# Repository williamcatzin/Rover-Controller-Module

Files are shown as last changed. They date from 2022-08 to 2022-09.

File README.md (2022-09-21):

# **Rover Controller Module**

The Rover Controller Module is an electronic control module (ECM) for a Mars rover prototype being developed by the AI Rover team from the Space Technologies At Cal (STAC). The PCB is a four-layer board consisting of an ESP32-WROOM32 module, BMI088 IMU breakout board, RFM69HCW transceiver module, UART header pin interface for three Roboclaw 2x7A motor controllers, and a SPI header pin interface for an external microprocessor such as an NVIDIA Jetson or Raspberry Pi. There’s also decoupling capacitors to suppress power supply noise and TVS diodes for safety and component protection. The PCB was designed using KiCAD and manufactured by JLCPCB. Top and bottom layers are signal planes. First middle layer is the ground plane and the second middle layer is the power plane. I've also placed three test points at the UART, I2C, and SPI serial buses respectively, mounting holes, and logos for aesthetics. Here’s the Rover Controller Module v1.

|||
|:-:|:-:|
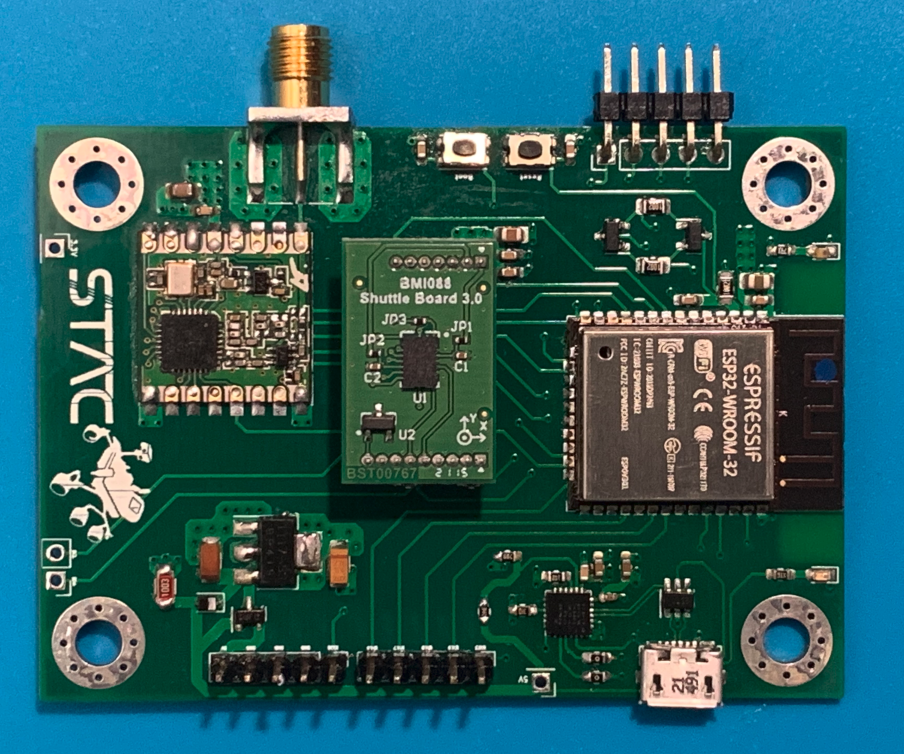
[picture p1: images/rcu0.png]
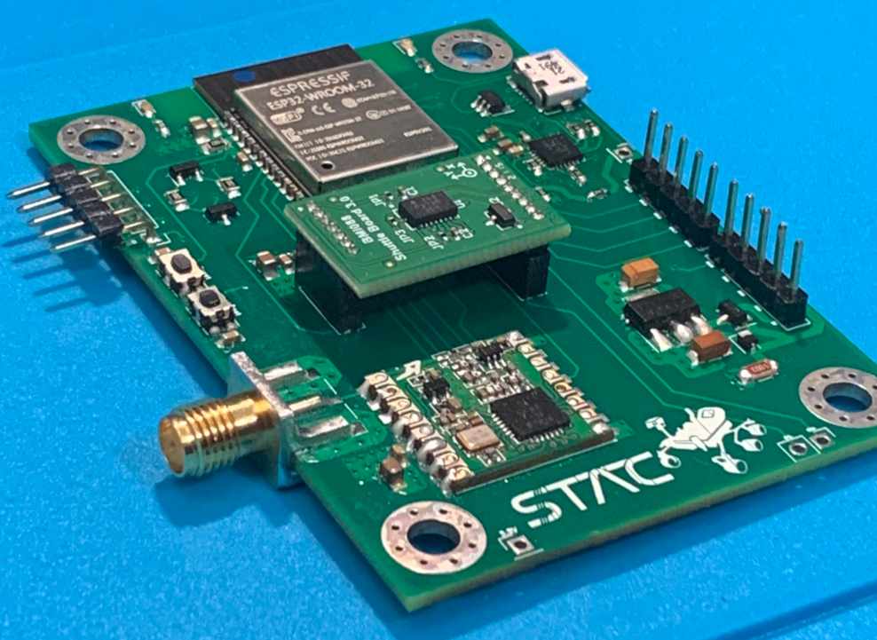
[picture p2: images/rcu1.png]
|||

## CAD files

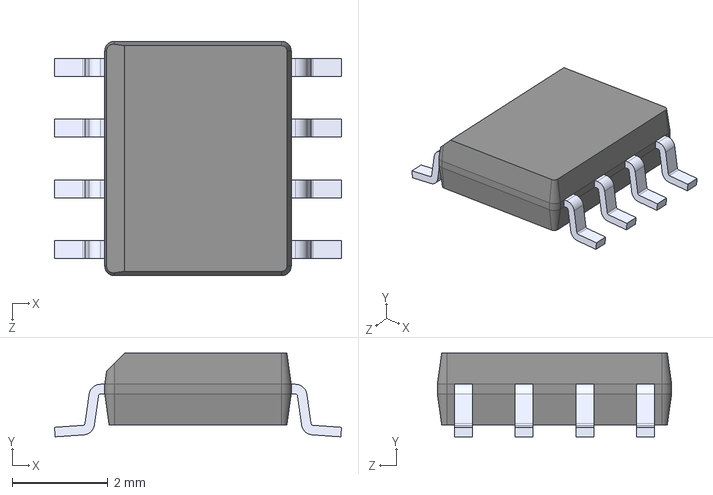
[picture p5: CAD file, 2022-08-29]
pcb_workspace/rover_controller/Regulator/SOIC127P600X175-8N.step
6.00 x 1.75 x 4.90 mm

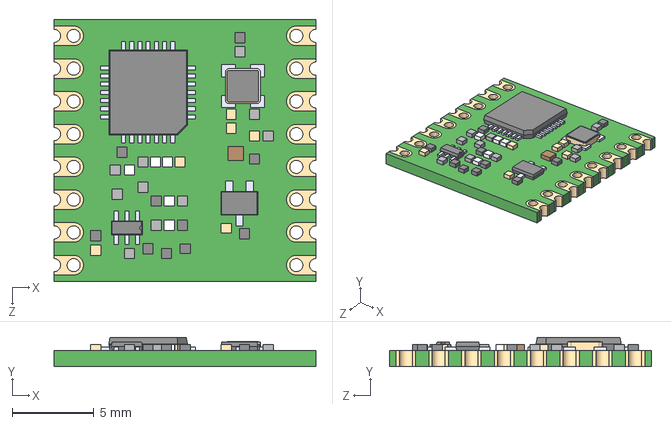
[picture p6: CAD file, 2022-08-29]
pcb_workspace/rover_controller/RFM69HCW/COM-13909.step
16.0 x 1.80 x 16.0 mm

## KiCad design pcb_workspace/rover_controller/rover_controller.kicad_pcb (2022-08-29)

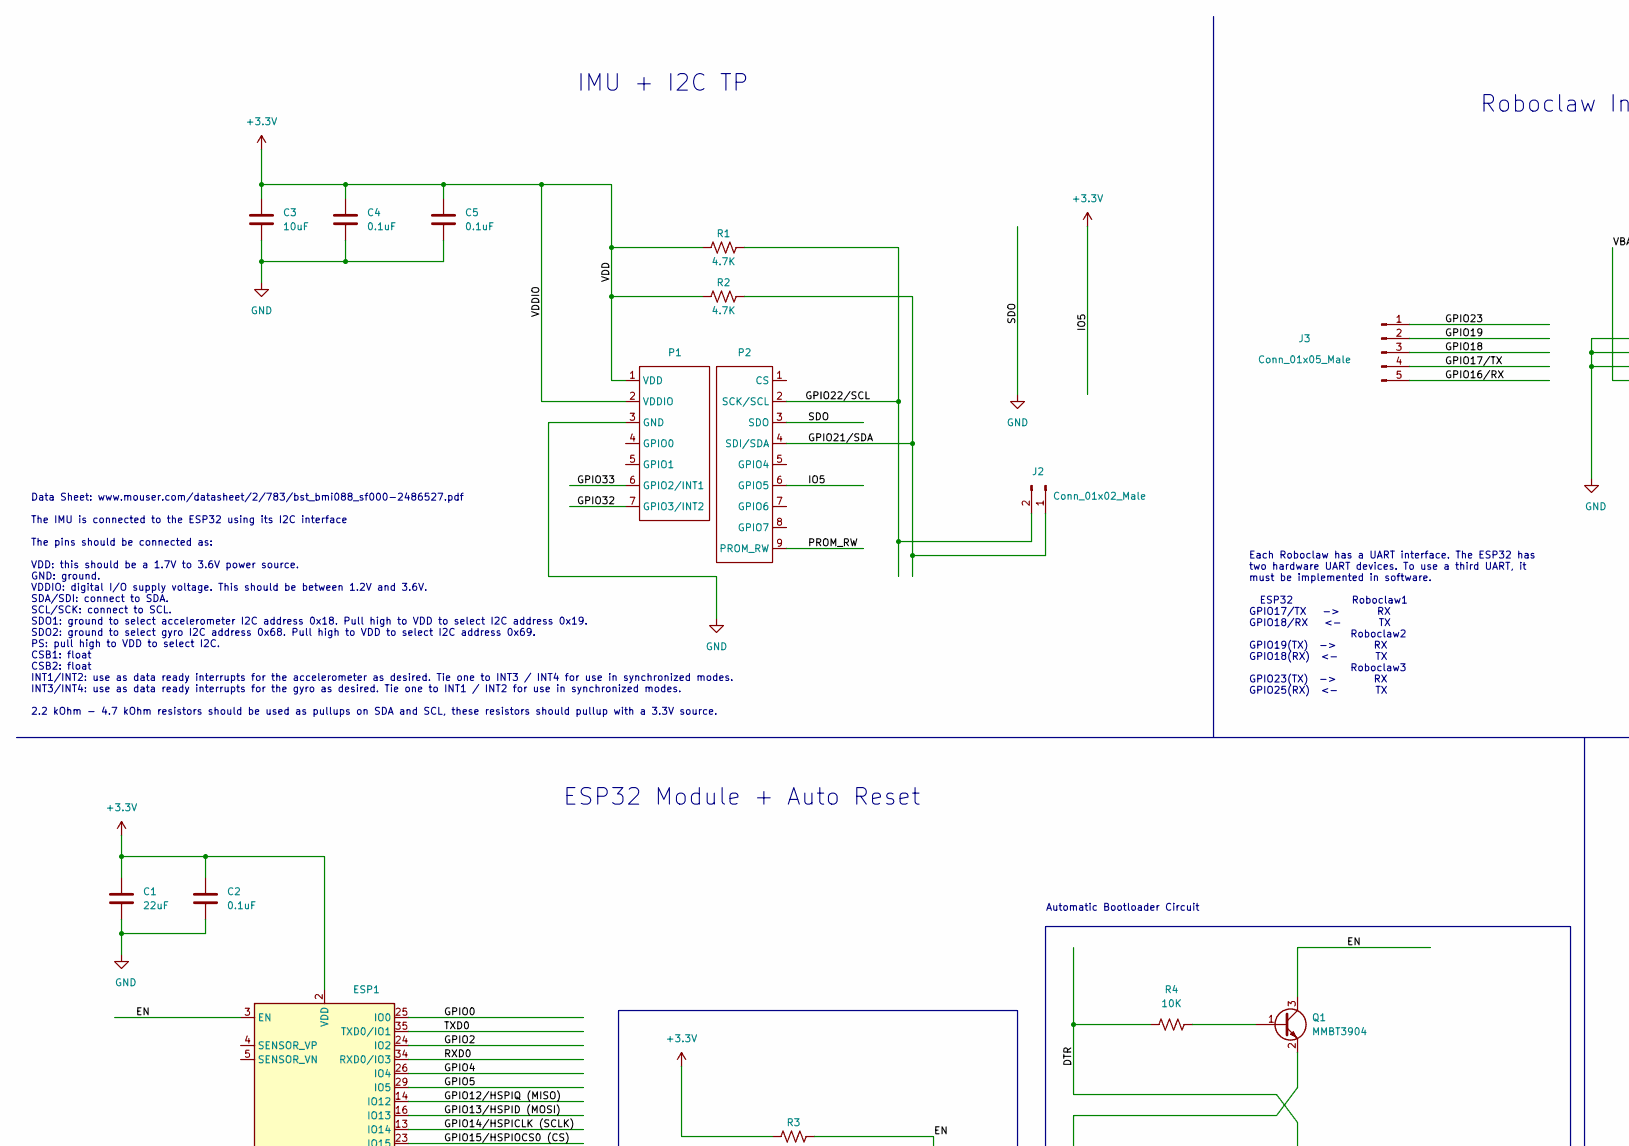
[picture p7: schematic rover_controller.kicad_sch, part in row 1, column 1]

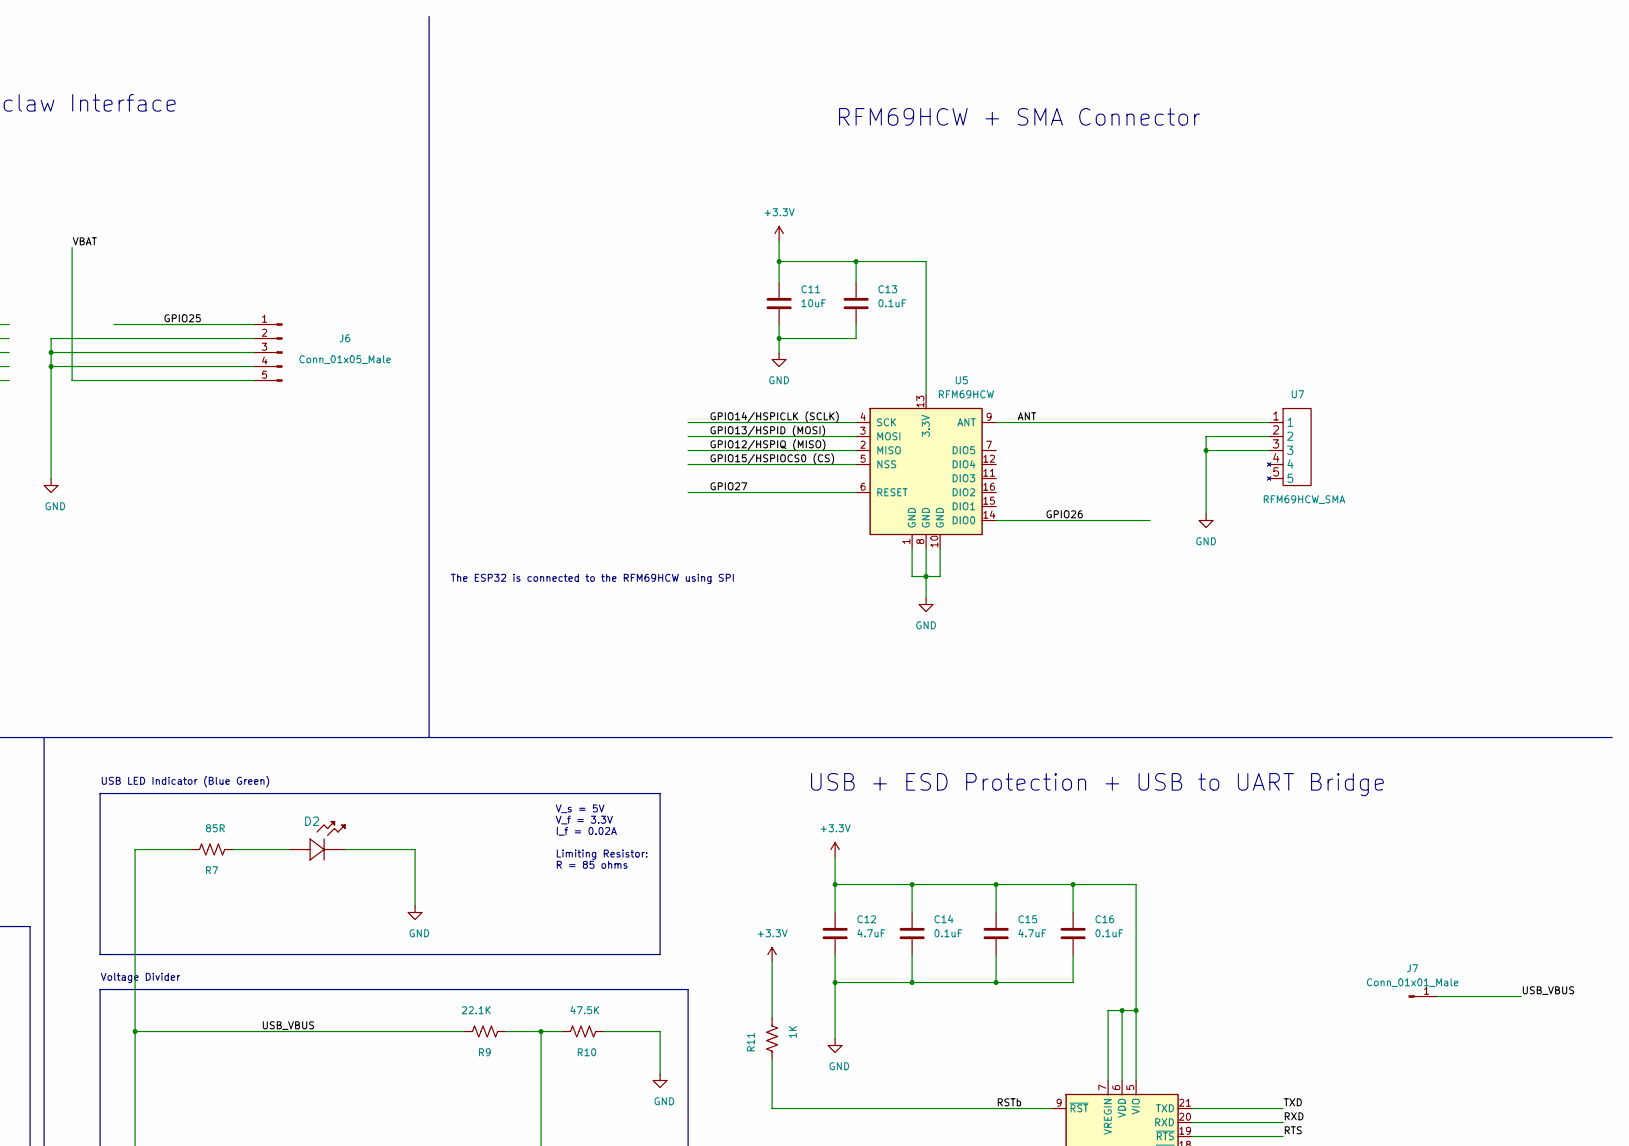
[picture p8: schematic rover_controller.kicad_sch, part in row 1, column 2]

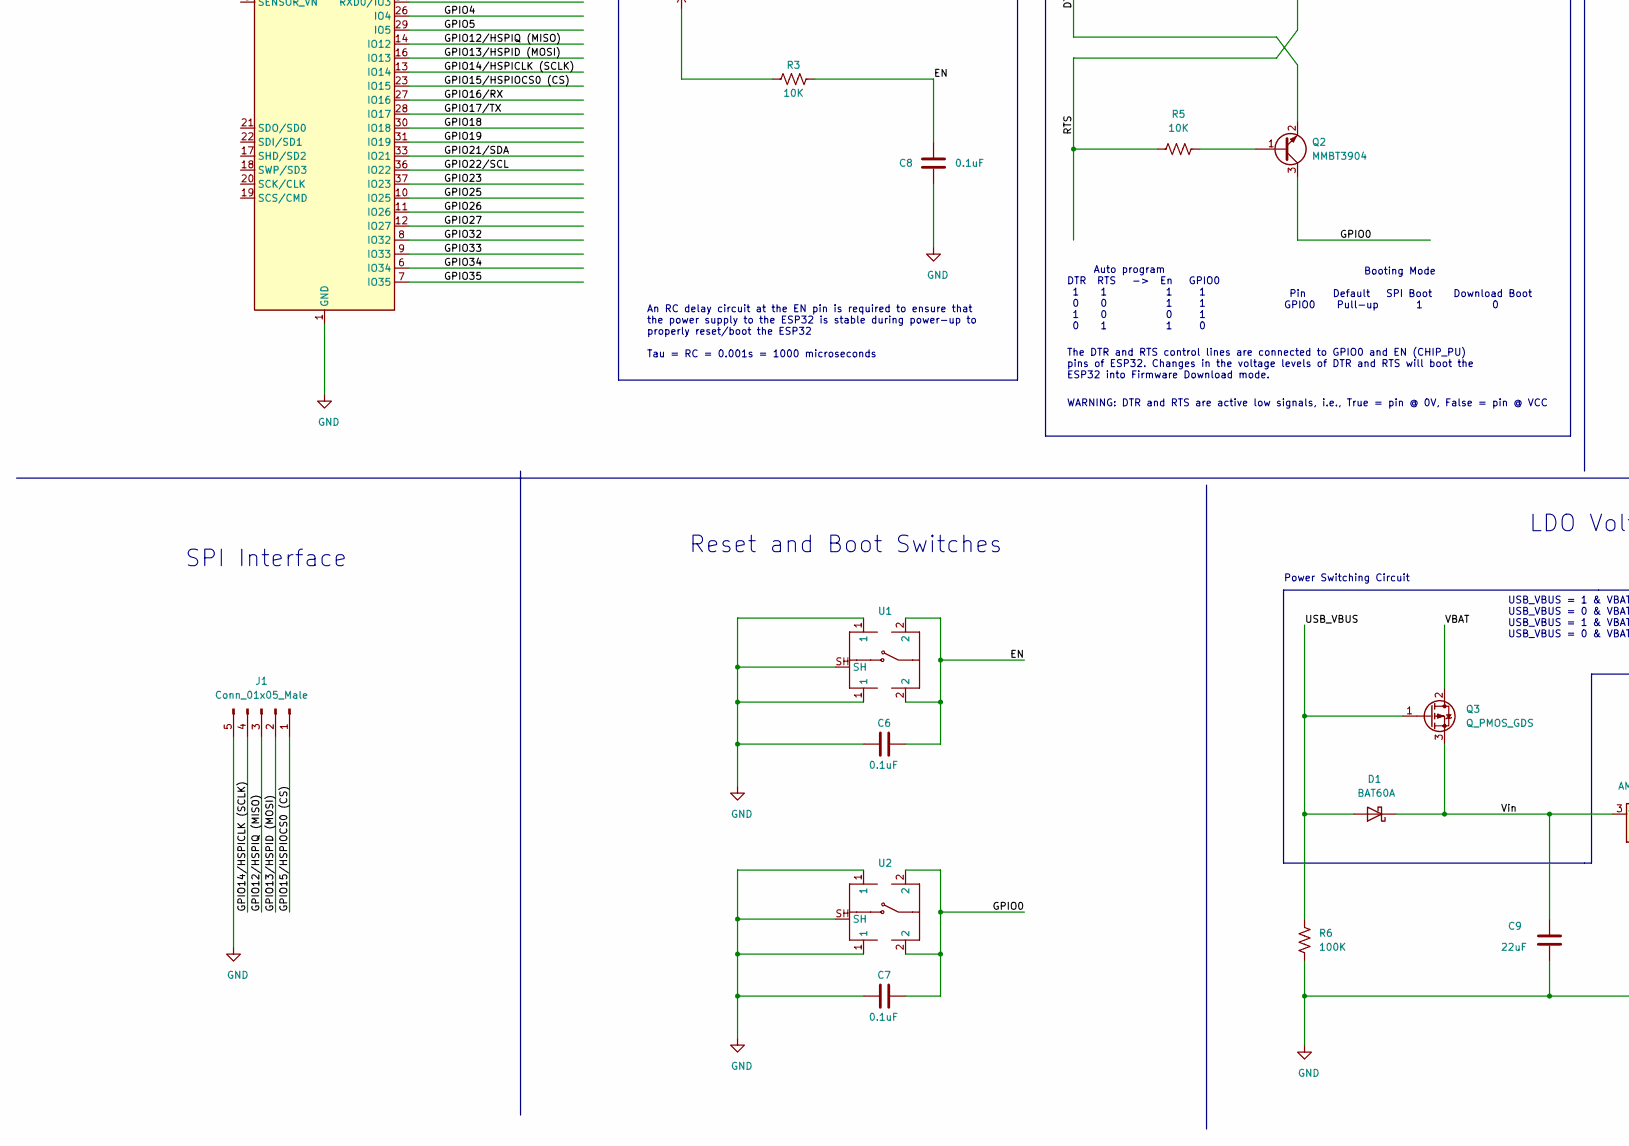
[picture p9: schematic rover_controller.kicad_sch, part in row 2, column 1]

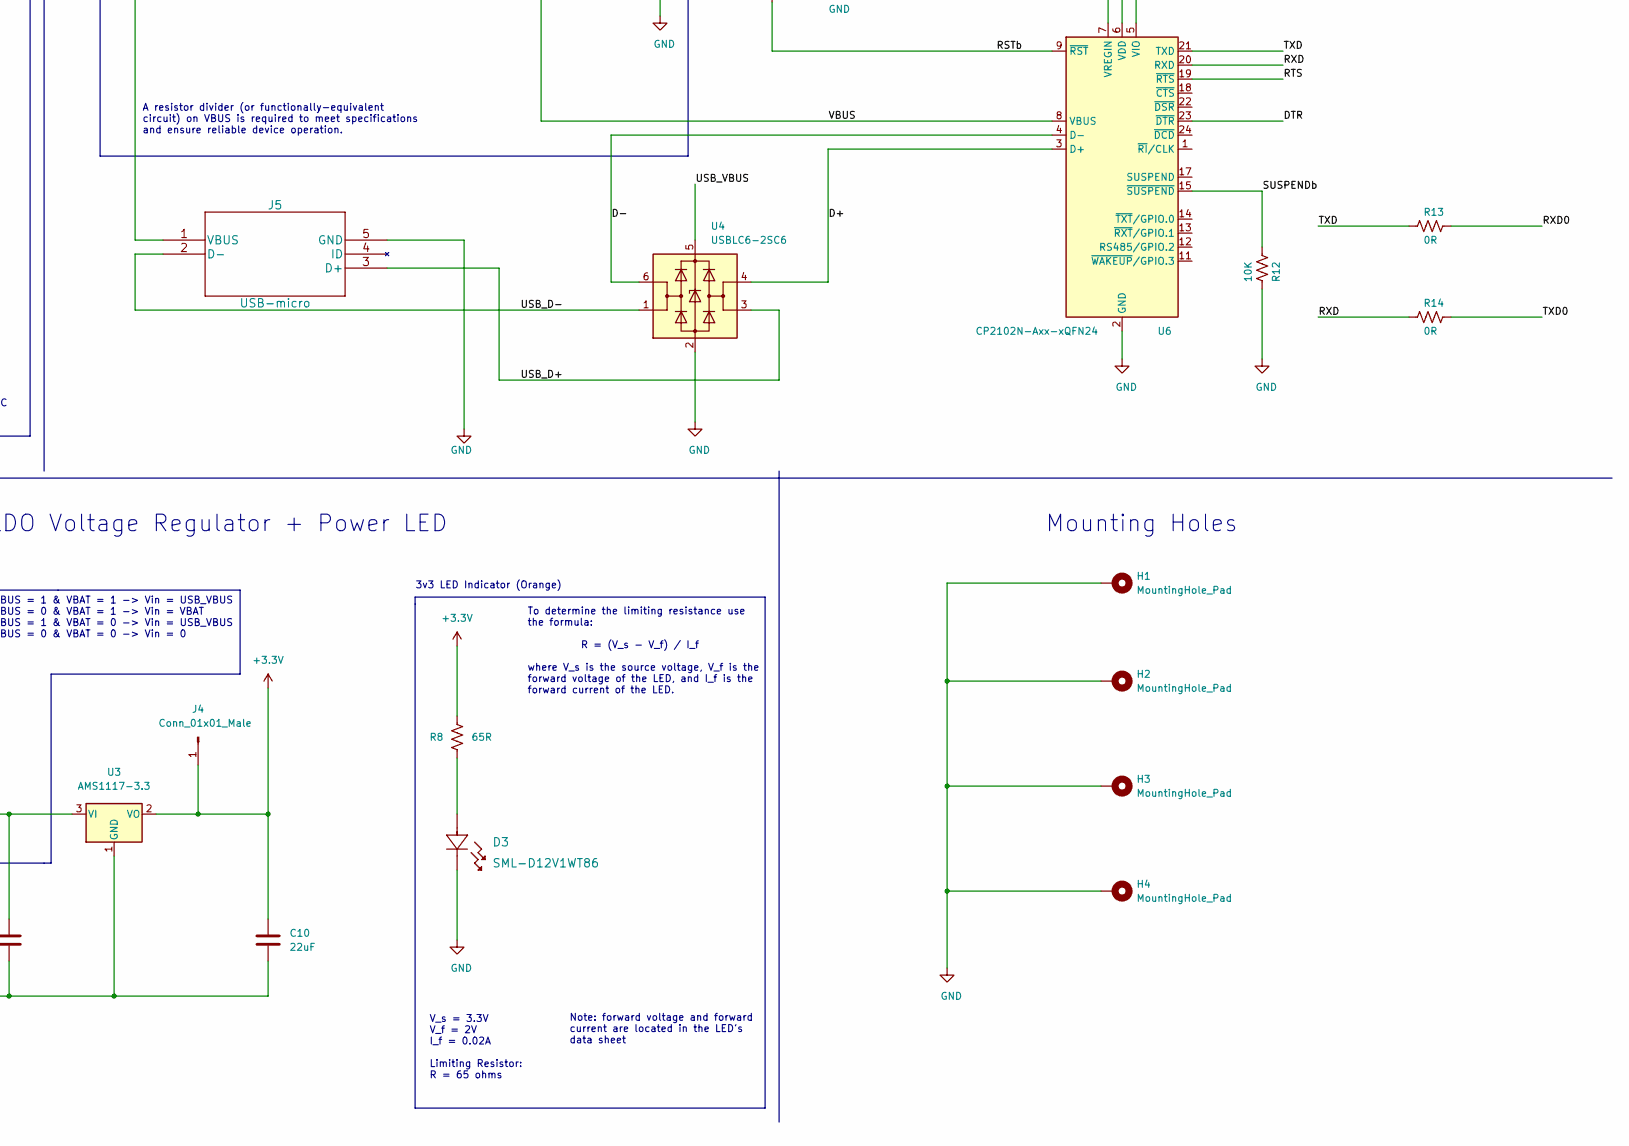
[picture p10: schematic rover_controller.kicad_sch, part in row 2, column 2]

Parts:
C1: 22uF; C_0805_2012Metric_Pad1.18x1.45mm_HandSolder
C2, C4, C5, C6, C7, C8, C13: 0.1uF; C_0603_1608Metric_Pad1.08x0.95mm_HandSolder
C3, C11: 10uF; C_0805_2012Metric_Pad1.18x1.45mm_HandSolder
C9, C10: 22uF; C_1206_3216Metric_Pad1.33x1.80mm_HandSolder
C12, C15: 4.7uF; C_0603_1608Metric_Pad1.08x0.95mm_HandSolder
C14, C16: 0.1uF; C_0402_1005Metric_Pad0.74x0.62mm_HandSolder
D1: BAT60A; D_SOD-323
D2, D3: SML-D12V1WT86; LED_0603_1608Metric_Pad1.05x0.95mm_HandSolder
ESP1: ESP32-WROOM-32
H1, H2, H3, H4: MountingHole_Pad; MountingHole_4.3mm_M4_Pad_Via
J1, J3, J6: Conn_01x05_Male; PinHeader_1x05_P2.54mm_Vertical
J2: Conn_01x02_Male; PinHeader_1x02_P2.54mm_Vertical
J4, J7: Conn_01x01_Male; PinHeader_1x01_P2.54mm_Vertical
J5: USB-micro; USB_Micro-B_Molex_47346-0001
P1: BST_Shuttleboard_Conn1; PinSocket_1x07_P1.27mm_Vertical
P2: BST_Shuttleboard_Conn2; PinSocket_1x09_P1.27mm_Vertical
Q1, Q2: MMBT3904; SOT-23
Q3: Q_PMOS_GDS; SOT-23
R1, R2: 4.7K; R_0603_1608Metric_Pad0.98x0.95mm_HandSolder
R3, R4, R5: 10K; R_0805_2012Metric_Pad1.20x1.40mm_HandSolder
R6: 100K; R_1206_3216Metric_Pad1.30x1.75mm_HandSolder
R7: 85R; R_0603_1608Metric_Pad0.98x0.95mm_HandSolder
R8: 65R; R_0603_1608Metric_Pad0.98x0.95mm_HandSolder
R9: 22.1K; R_0603_1608Metric_Pad0.98x0.95mm_HandSolder
R10: 47.5K; R_0603_1608Metric_Pad0.98x0.95mm_HandSolder
R11: 1K; R_0603_1608Metric_Pad0.98x0.95mm_HandSolder
R12: 10K; R_0603_1608Metric_Pad0.98x0.95mm_HandSolder
R13, R14: 0R; R_0603_1608Metric_Pad0.98x0.95mm_HandSolder
U1, U2: KMR_SW_SPST; SW_Push_1P1T-SH_NO_CK_KMR2xxG
U3: AMS1117-3.3; SOT-223-3_TabPin2
U4: USBLC6-2SC6; SOT-23-6
U5: RFM69HCW
U6: CP2102N-Axx-xQFN24; QFN-24-1EP_4x4mm_P0.5mm_EP2.6x2.6mm
U7: RFM69HCW_SMA; 60312202114509

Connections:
+3V3: C1.1, C2.1, C3.1, C4.1, C5.1, C10.1, C11.1, C12.1, C13.1, C14.1, C15.1, C16.1, ESP1.2 (VDD), J4.1, P1.1 (VDD), P1.2 (VDDIO), P2.6 (GPIO5), R1.1, R2.1, R3.1, R8.1, R11.2, U3.2 (VO), U5.13 (3.3V), U6.5 (VIO), U6.6 (VDD), U6.7 (VREGIN)
/ANT: U5.9 (ANT), U7.1
/D+: U4.4 (I/O2), U6.3 (D+)
/D-: U4.6 (I/O1), U6.4 (D-)
/DTR: Q2.2 (E), R4.1, U6.23 (~DTR)
/EN: C6.2, C8.1, ESP1.3 (EN), Q1.3 (C), R3.2, U1.2
/GPIO0: C7.2, ESP1.25 (IO0), Q2.3 (C), U2.2
/GPIO2: ESP1.24 (IO2)
/GPIO4: ESP1.26 (IO4)
/GPIO5: ESP1.29 (IO5)
/GPIO12/HSPIQ (MISO): ESP1.14 (IO12), J1.3, U5.2 (MISO)
/GPIO13/HSPID (MOSI): ESP1.16 (IO13), J1.2, U5.3 (MOSI)
/GPIO14/HSPICLK (SCLK): ESP1.13 (IO14), J1.4, U5.4 (SCK)
/GPIO15/HSPIOCS0 (CS): ESP1.23 (IO15), J1.1, U5.5 (NSS)
/GPIO16/RX: ESP1.27 (IO16), J3.5
/GPIO17/TX: ESP1.28 (IO17), J3.4
/GPIO18: ESP1.30 (IO18), J3.3
/GPIO19: ESP1.31 (IO19), J3.2
/GPIO21/SDA: ESP1.33 (IO21), J2.1, P2.4 (SDI/SDA), R2.2
/GPIO22/SCL: ESP1.36 (IO22), J2.2, P2.2 (SCK/SCL), R1.2
/GPIO23: ESP1.37 (IO23), J3.1
/GPIO25: ESP1.10 (IO25), J6.1
/GPIO26: ESP1.11 (IO26), U5.14 (DIO0)
/GPIO27: ESP1.12 (IO27), U5.6 (RESET)
/GPIO32: ESP1.8 (IO32), P1.7 (GPIO3/INT2)
/GPIO33: ESP1.9 (IO33), P1.6 (GPIO2/INT1)
/GPIO34: ESP1.6 (IO34)
/GPIO35: ESP1.7 (IO35)
/PROM_RW: P2.9 (PROM_RW)
/RSTb: R11.1, U6.9 (~RST)
/RTS: Q1.2 (E), R5.1, U6.19 (~RTS)
/RXD: R14.2, U6.20 (RXD)
/RXD0: ESP1.34 (RXD0/IO3), R13.1
/SUSPENDb: R12.2, U6.15 (~SUSPEND)
/TXD: R13.2, U6.21 (TXD)
/TXD0: ESP1.35 (TXD0/IO1), R14.1
/USB_D+: J5.3 (D+), U4.3 (I/O2)
/USB_D-: J5.2 (D-), U4.1 (I/O1)
/USB_VBUS: D1.2 (A), J5.1 (VBUS), J7.1, Q3.1 (G), R6.1, R7.1, R9.1, U4.5 (VBUS)
/VBAT: J6.5, Q3.2 (D)
/VBUS: R9.2, R10.2, U6.8 (VBUS)
/Vin: C9.1, D1.1 (K), Q3.3 (S), U3.3 (VI)
GND: C1.2, C2.2, C3.2, C4.2, C5.2, C6.1, C7.1, C8.2, C9.2, C10.2, C11.2, C12.2, C13.2, C14.2, C15.2, C16.2, D2.1, D3.1, ESP1.1 (GND), ESP1.15 (GND), ESP1.38 (GND), ESP1.39 (GND), H1.1, H2.1, H3.1, H4.1, J1.5, J5.5 (GND), J6.2, J6.3, J6.4, P1.3 (GND), P2.3 (SDO), R6.2, R10.1, R12.1, U1.1, U1.SH, U2.1, U2.SH, U3.1 (GND), U4.2 (GND), U5.1 (GND), U5.8 (GND), U5.10 (GND), U6.2 (GND), U6.25 (GND), U7.2, U7.3
unnamed: D2.2, R7.2
unnamed: D3.2, R8.2
unnamed: Q1.1 (B), R4.2
unnamed: Q2.1 (B), R5.2

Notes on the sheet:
SPI Interface
3v3 LED Indicator (Orange)
Each Roboclaw has a UART interface. The ESP32 has two hardware UART devices. To use a third UART, it must be implemented in software. ESP32 Roboclaw1 GPIO17/TX -> RX GPIO18/RX <- TX Roboclaw2 GPIO19(TX) -> RX GPIO18(RX) <- TX Roboclaw3 GPIO23(TX) -> RX GPIO25(RX) <- TX
Note: forward voltage and forward current are located in the LED's data sheet
An RC delay circuit at the EN pin is required to ensure that the power supply to the ESP32 is stable during power-up to properly reset/boot the ESP32 Tau = RC = 0.001s = 1000 microseconds
The ESP32 is connected to the RFM69HCW using SPI
Power Switching Circuit
A resistor divider (or functionally-equivalent circuit) on VBUS is required to meet specifications and ensure reliable device operation.
Mounting Holes
IMU + I2C TP
WARNING: DTR and RTS are active low signals, i.e., True = pin @ 0V, False = pin @ VCC
USB + ESD Protection + USB to UART Bridge
USB_VBUS = 1 & VBAT = 1 -> Vin = USB_VBUS USB_VBUS = 0 & VBAT = 1 -> Vin = VBAT USB_VBUS = 1 & VBAT = 0 -> Vin = USB_VBUS USB_VBUS = 0 & VBAT = 0 -> Vin = 0
The DTR and RTS control lines are connected to GPIO0 and EN (CHIP_PU) pins of ESP32. Changes in the voltage levels of DTR and RTS will boot the ESP32 into Firmware Download mode.
RFM69HCW + SMA Connector
LDO Voltage Regulator + Power LED
V_s = 5V V_f = 3.3V I_f = 0.02A Limiting Resistor: R = 85 ohms
To determine the limiting resistance use the formula: R = (V_s - V_f) / I_f where V_s is the source voltage, V_f is the forward voltage of the LED, and I_f is the forward current of the LED.
Booting Mode Pin Default SPI Boot Download Boot GPIO0 Pull-up 1 0
Auto program DTR RTS -> En GPIO0 1 1 1 1 0 0 1 1 1 0 0 1 0 1 1 0
Automatic Bootloader Circuit
Roboclaw Interface
Voltage Divider
ESP32 Module + Auto Reset
Reset and Boot Switches
USB LED Indicator (Blue Green)
V_s = 3.3V V_f = 2V I_f = 0.02A Limiting Resistor: R = 65 ohms
Data Sheet: www.mouser.com/datasheet/2/783/bst_bmi088_sf000-2486527.pdf The IMU is connected to the ESP32 using its I2C interface The pins should be connected as: VDD: this should be a 1.7V to 3.6V power source. GND: ground. VDDIO: digital I/O supply voltage. This should be between 1.2V and 3.6V. S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

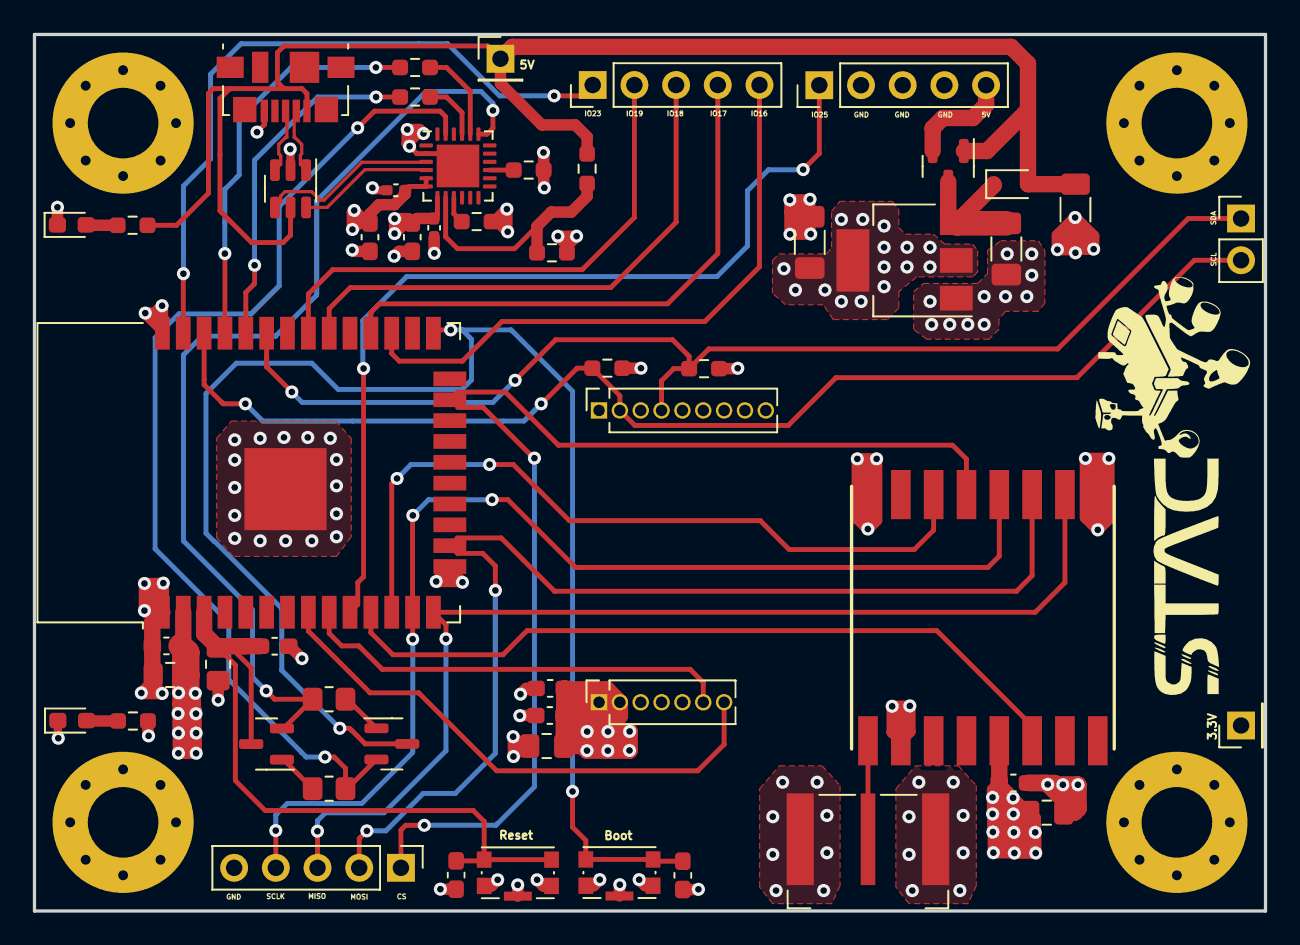
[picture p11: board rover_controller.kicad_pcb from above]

Board: 4 copper layers, 75.0 x 53.4 mm, 57 parts (0 on the bottom side), 41 nets.

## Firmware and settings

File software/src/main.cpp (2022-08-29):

//Includes required to use Roboclaw library
#include "RoboClaw.h"

RoboClaw roboclaw(&Serial2, 10000);



#define ROBOCLAW1 0x80
#define ROBOCLAW2 0x81
#define ROBOCLAW3 0x82

void setup() {
  //Open roboclaw serial ports
  roboclaw.begin(38400);
}

void loop() {
  roboclaw.ForwardM1(0x80, 64); //start Motor1 forward at half speed
  delay(2000);
  roboclaw.ForwardM1(0x80, 0); //start Motor1 forward at half speed
  delay(2000);

  roboclaw.ForwardM1(0x81, 64); //start Motor1 forward at half speed
  delay(2000);
  roboclaw.ForwardM1(0x81, 0); //start Motor1 forward at half speed
  delay(2000);

  roboclaw.ForwardM1(0x82, 64); //start Motor1 forward at half speed
  delay(2000);
  roboclaw.ForwardM1(0x82, 0); //start Motor1 forward at half speed
  delay(2000);  
}
